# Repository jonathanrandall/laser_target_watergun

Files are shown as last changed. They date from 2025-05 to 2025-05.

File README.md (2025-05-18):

# laser_target_watergun
Laser Targetting watergun with esp32 cam and esp32 controlling the laser module.

[Explanatory video](https://youtu.be/Ic2vv7IDxok)

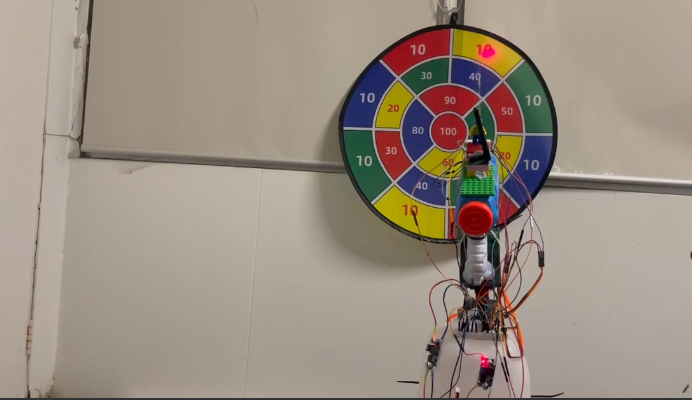
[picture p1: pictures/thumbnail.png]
Demo Video (https://youtu.be/Ic2vv7IDxok)


__Note:__ The __User_Setup.h__ file contains the configuration for the elecrow red display with the esp32. If using cheap yellow display need to set TFT_BL to -1. This would normally be set to 21, but pin 21 is held high by a pullup resistor, so the screen will still work.

## Directories:
__3d print files:__ This contains the files to 3d print the handset.

__schematics:__ This contains the schematics for the wiring for both the watergun side and the tft side

__tft_side_watergun_v2:__ The software for the tft side with the laser module attached

__watergun_side_v3:__ The software for the watergun side

__________________________________________

## Bill of Materials:

### Laser module with TFT screen
1. Laser Module. Note: laser module is not exaclty the same as laser pointer. Search amazon or aliexpress for "laser module". I'm using this one: [dot laser module](https://www.amazon.com.au/650nm-Laser-Module-Adjustable-Industrial/dp/B07PV4BWVH/)
2. TFT with esp32 connected. I'm using the elecrow red display, but you can use a cheap yellow display or a tft with an esp32. I'm using this one: [elecrow red display](https://www.elecrow.com/esp32-display-2-8-inch-hmi-display-spi-tft-lcd-touch-screen.html)
3. Push buttons x 2.
4. Pull up resistors X 2. I'm using 6.8 kohm, but anywhere from 5k to 15k should be ok.
5. 18650 battery and battery holder
6. Jumper wires, 3d printer,  hot glue, solder, etc...

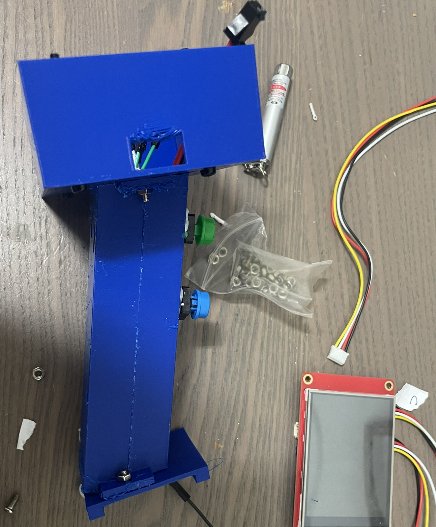
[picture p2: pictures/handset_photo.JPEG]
laser_module_handset


### Water gun side with camera
1. Esp32 cam. I'm using the AI thinker but any esp32 cam should be ok.
2. Electric wategun. The one I'm using isn't in production anymore. But any electric watergun that can fit easily onto a servo pan-tilt mechanism. Some might have an awkward shape at the bottom that makes it difficult. So keep this in mind. Also should have easy access to battery wiring should work.
3. High torque Servos x 2. I'm using 25kg/cm servos. You can get these from aliexpress.
4. Servo pan-tilt mechanism. One for size mg995 servo should work for the 25kg/cm servos from aliexpress. Don't get the smaller ones for the sg90 servos.
5. Buck converters X 2: one for the 6.5V supply for the servos and one for the 5V supply for the esp32 and watergun. I'm using the LM2596.
6. TB6612FNG motor controller.
7. Small breadboard.
8. Battery. I'm using a 2S lipo. But anything that works with the buck converters should be ok.
9. Jumper cables, hot glue, etc... 

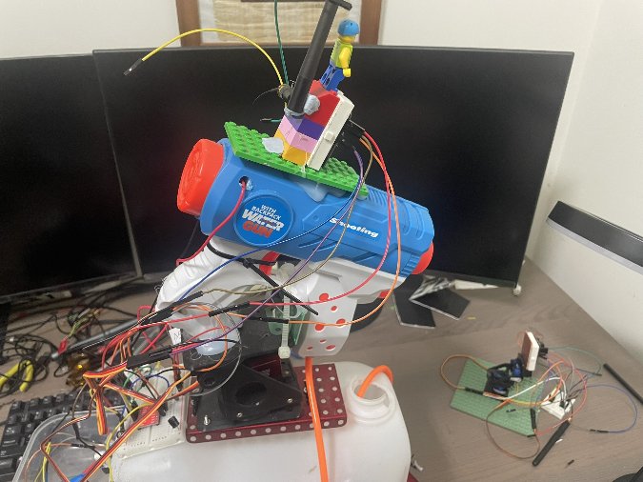
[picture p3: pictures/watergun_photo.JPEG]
watergun_side


previous videos on wategun are at:

[esp32 watergun](https://youtu.be/s5WNyXVWSS8)

[esp32 watergun with tracking](https://youtu.be/NK1wj7sDLNc)

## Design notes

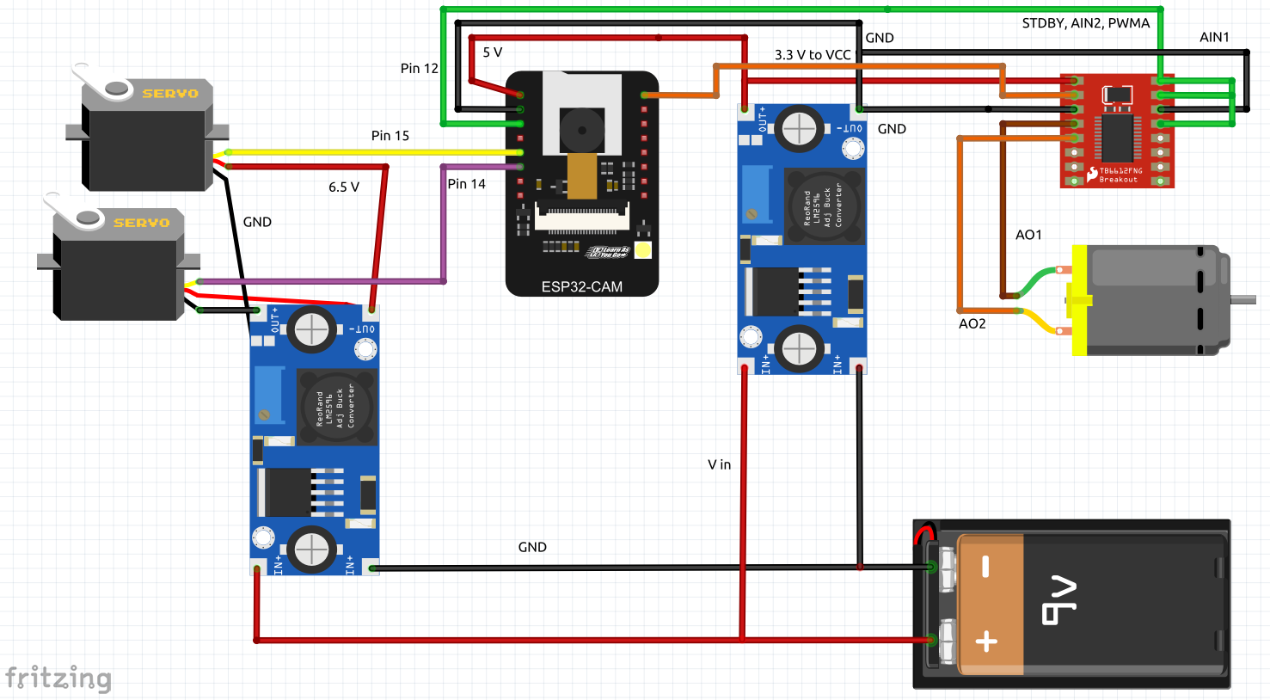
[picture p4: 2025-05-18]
schematics/watergun_schematic_labeled.png

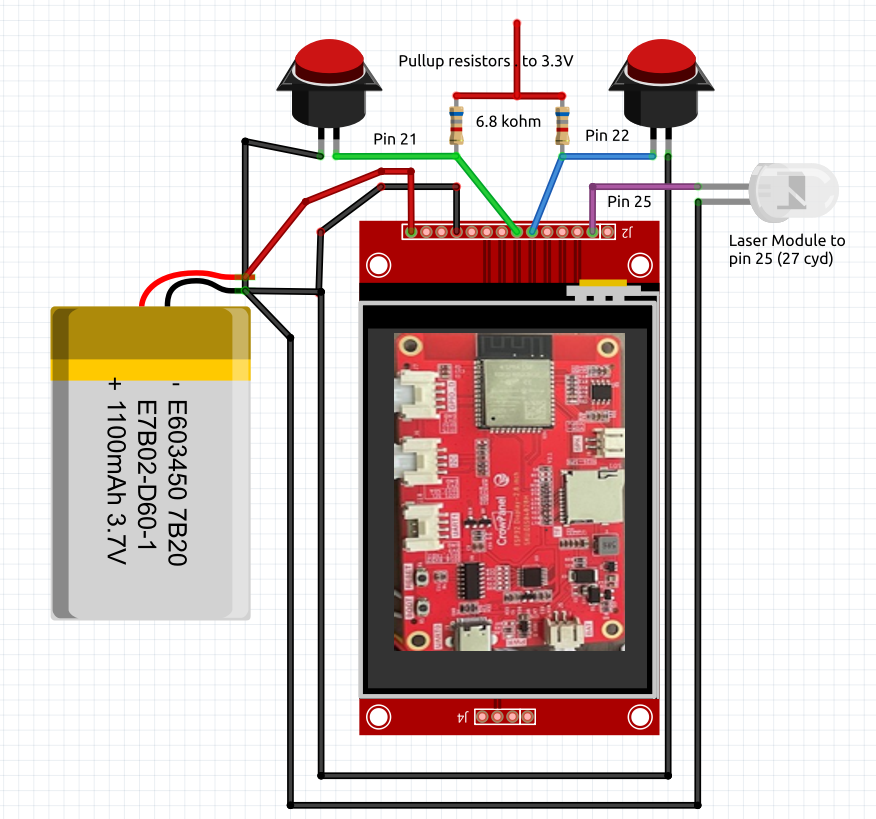
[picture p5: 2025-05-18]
schematics/tft_schematic_labeled_2.png

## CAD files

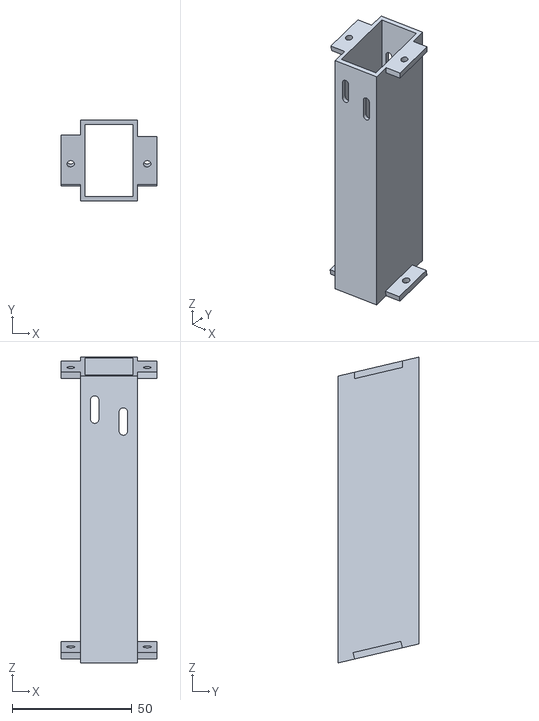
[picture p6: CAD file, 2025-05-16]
3d print files/handle_laser-Body.stl
40.0 x 34.0 x 128.0

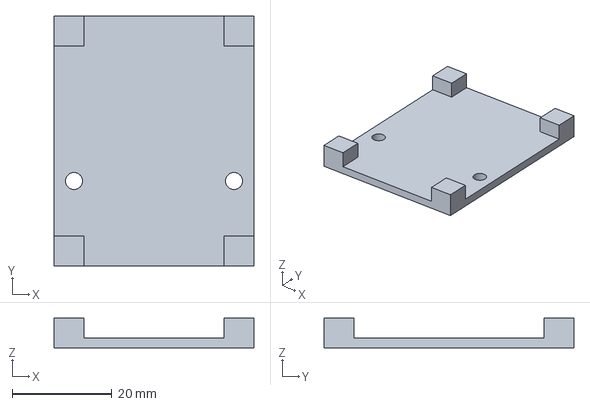
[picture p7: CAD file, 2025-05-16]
3d print files/handle_laser.FCStd
40.0 x 50.0 x 6.00 mm

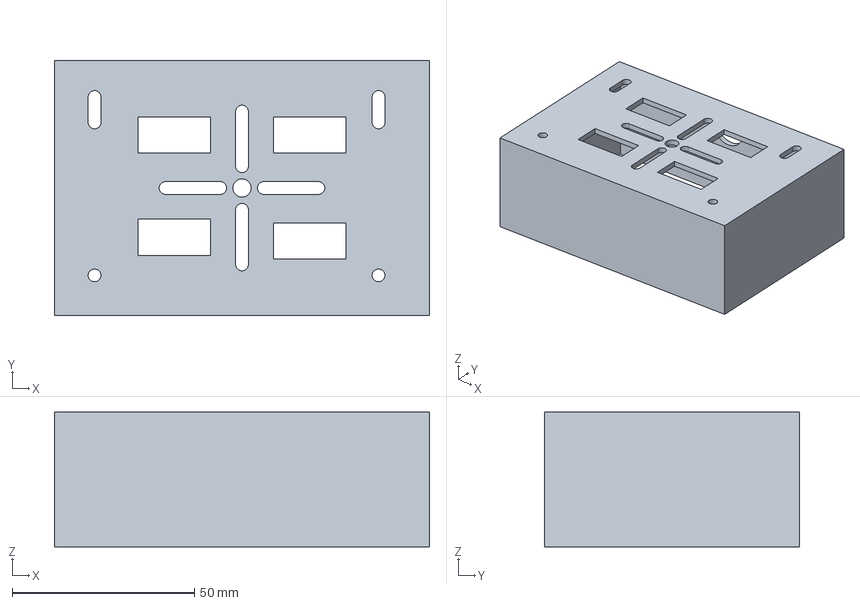
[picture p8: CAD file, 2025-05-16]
3d print files/box laser.FCStd
103.0 x 70.0 x 37.0 mm

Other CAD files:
3d print files/bottom_laser-Body.stl
3d print files/box_laser-Body.stl

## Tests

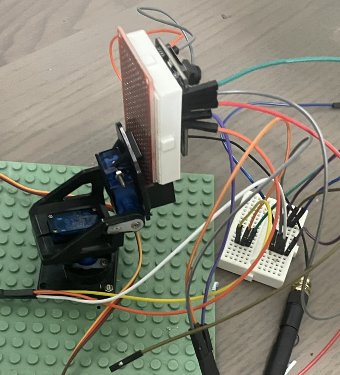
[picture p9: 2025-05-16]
pictures/test_rig_photo.JPEG

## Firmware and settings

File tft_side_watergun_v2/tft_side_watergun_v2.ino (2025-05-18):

#include <WiFi.h>
#include <TFT_eSPI.h>  // TFT library (make sure to include the correct library for your TFT display)
#include <HTTPClient.h>
#include <TJpg_Decoder.h>
#include "tft_stuff.h"




// const char* stream_url ="http://jonny-ubuntu.local:81/";// "http://192.168.4.1:81/stream";
// const char* stream_url ="http://192.168.4.1:81/stream";
// const char* stream_url = "http://rpizero.local:7123/stream11.mjpg";



// const char* ssid = "ESP32_CAM_AP";
// const char* password = "12345678";



#define PART_BOUNDARY "123456789000000000000987654321"
static const char* _STREAM_CONTENT_TYPE = "multipart/x-mixed-replace;boundary=" PART_BOUNDARY;
static const char* _STREAM_BOUNDARY = "\r\n--" PART_BOUNDARY "\r\n";
static const char* _STREAM_PART = "Content-Type: image/jpeg\r\nContent-Length ";//%u\r\n\r\n";

bool my_touch_read(uint16_t *x, uint16_t *y){
  bool touched = tft.getTouch(x,y);
  return touched;
}

bool tft_output(int16_t x, int16_t y, uint16_t w, uint16_t h, uint16_t* bitmap){
  if ( y >= tft.height() ) return 0;
  // tft.pushImage(x, y, w, h, bitmap);
  tft.pushImage(x, y, h, w, bitmap);
  return 1;
}

void processImage(uint8_t* image_data, size_t length) {
  // Serial.println("Processing full image...");
  TJpgDec.drawJpg(0, 0, (const uint8_t*)image_data, length);
  // Display or process the complete image here (e.g., render it on the TFT)
}

void drawJpeg(uint8_t* image_data, size_t length) {
  // Serial.println("Processing full image...");
  TJpgDec.drawJpg(0, 0, (const uint8_t*)image_data, length);
  // Display or process the complete image here (e.g., render it on the TFT)
}

void init_wifi_old()
{
  WiFi.mode(WIFI_STA);
  WiFi.begin(ssid, password);
  while (WiFi.status() != WL_CONNECTED) {
    delay(1000);
    Serial.println("Connecting to WiFi...");
  }
    Serial.println("");
    Serial.println("WiFi connected");
    Serial.println("IP address: ");
    Serial.println(WiFi.localIP());
    Serial.println("");
    return;

    
}

void init_wifi()
{
  WiFi.mode(WIFI_STA);
  
  // Attempt first SSID
  WiFi.begin(ssid, password);
  unsigned long startAttemptTime = millis();
  while (WiFi.status() != WL_CONNECTED && millis() - startAttemptTime < 10000) {
    delay(500);
    Serial.println("Connecting to primary WiFi...");
  }

  // If not connected after 5 seconds, try second SSID
  if (WiFi.status() != WL_CONNECTED) {
    Serial.println("Failed to connect to primary WiFi. Trying backup...");
    // WiFi.disconnect(true);
    // delay(80);
    WiFi.begin(ssid2, password2);
    startAttemptTime = millis();
    while (WiFi.status() != WL_CONNECTED && millis() - startAttemptTime < 5000) {
      delay(500);
      Serial.println("Connecting to backup WiFi...");
    }
  }

  // Final connection result
  if (WiFi.status() == WL_CONNECTED) {
    Serial.println("");
    Serial.println("WiFi connected");
    Serial.println("IP address: ");
    Serial.println(WiFi.localIP());
    Serial.println("");
  } else {
    Serial.println("Failed to connect to any WiFi network.");
  }
}


bool fire_done;
int unsigned long last_read_l;
int unsigned long last_read_f;
int unsigned long last_touch;

uint16_t px=0, py=0;
bool l_button_pushed, prev_l_button_pushed;
bool f_button_pushed, prev_f_button_pushed;
bool laser_on;
// HTTPClient http;
// WiFiClient* stream = nullptr;
void setup() {
  Serial.begin(115200);
  
  tft.init();
  tft.fillScreen(TFT_BLACK);  // Clear screen
  

  init_wifi();

    // Initialize the TFT screen
  tft.init();
  tft.setRotation(1);
  tft.setTextColor(TFT_WHITE,TFT_BLACK); 
  tft.fillScreen(TFT_BLACK);
  // tft.invertDisplay(true); //original and aliexpress but not elecros
  tft.setSwapBytes(true);
  tft.fillScreen(TFT_GREEN);
  delay(200);
  tft.fillScreen(TFT_BLACK);
  tft.setTextFont(4);
  tft.writecommand(ILI9341_GAMMASET); //Gamma curve selected for original one only but no aliexpress or elecrow.
  tft.writedata(2);
  delay(120);
  // tft.writecommand(ILI9341_GAMMASET); //Gamma curve selected
  tft.writedata(1);
  // analogWrite(21,64);

  TJpgDec.setJpgScale(1);
  TJpgDec.setCallback(tft_output);

  pinMode(laser_button, INPUT_PULLUP);
  pinMode(22, INPUT);
  pinMode(25, OUTPUT);

  xTaskCreatePinnedToCore(
       image_stream, /* Function to implement the task */
       "is",    /* Name of the task */
       1024*15,            /* Stack size in words */
       NULL,            /* Task input parameter */
       1,               /* Priority of the task */
       NULL,     /* Task handle. */
       1);              /* Core where the task should run */
 
//  xTaskCreatePinnedToCore(
//        laser_controls, /* Function to implement the task */
//        "lc",    /* Name of the task */
//        1024*5,            /* Stack size in words */
//        NULL,            /* Task input parameter */
//        1,               /* Priority of the task */
//        NULL,     /* Task handle. */
//        1);              /* Core where the task should run */
 

  // http.begin(stream_url);
  // int httpCode = http.GET();

  // if (httpCode == HTTP_CODE_OK) {
  //   stream = http.getStreamPtr();
  //   } else {
  //   Serial.printf("Failed to connect to stream, HTTP code: %d\n", httpCode);
  // }
  
  // Start the image stream
  // startStream();
  fire_done = false;
  last_read_l = millis();
  last_read_f = millis();
  last_touch = millis();

  prev_l_button_pushed = !digitalRead(laser_button); // digitalRead(laser_button);
  prev_f_button_pushed = !digitalRead(fire_button); //digitalRead(f_button);
  Serial.println("prev_l_button");
  Serial.println(prev_l_button_pushed);
  delay(1000);
  
  
}

// uint8_t *downloadBuffer = NULL;
//   int downloadBufferLength = 0;

//   uint8_t *mCurrentFrameBuffer = NULL;
//     size_t mCurrentFrameLength = 0;
//     size_t mCurrentFrameBufferLength = 0;
 void laser_controls(void *args){
  int unsigned long last_read_l;
  int unsigned long last_read_f;
  int unsigned long last_touch;
  last_read_l = millis();
  last_read_f = millis();
  last_touch = millis();
  uint16_t px=0, py=0;
  bool l_button_pushed, prev_l_button_pushed;
  bool f_button_pushed, prev_f_button_pushed;
  bool laser_on;
  prev_l_button_pushed = !digitalRead(laser_button); // digitalRead(laser_button);
  prev_f_button_pushed = !digitalRead(fire_button); //digitalRead(f_button);
  while (true){
    l_button_pushed = !digitalRead(laser_button); //high is off
    f_button_pushed = !digitalRead(fire_button); //high is off
    laser_on = digitalRead(laser);
    // Serial.print("prev l button");
    // Serial.println(prev_f_button_pushed);
    // Serial.print("l button");
    // Serial.println(l_button_pushed);
    if (millis() - last_read_l > 100 && !l_button_pushed && l_button_pushed!=prev_l_button_pushed){
      digitalWrite(laser, !laser_on); //toggle laser
      Serial.println("laser toggled");
      last_read_l = millis();
    }

    if (millis() - last_read_f > 1000 && laser_on && !f_button_pushed && f_button_pushed!=prev_f_button_pushed){
      Serial.println("target gotten");
      spray_target_with_water();
      last_read_f = millis();
      
      // sendMessage("target_get");
    }

    //squirt action

    if (!laser_on && f_button_pushed && !f_button_pushed!=prev_f_button_pushed){
      Serial.println("squirt");
      sendMessage("squirt");
      last_read_f = millis();
      
      // sendMessage("target_get");
    }

    /*
    //the my_touch_read needs a semaphore: TODO
    if (millis() - last_touch > 200 && my_touch_read(&px, &py)){
      sendMessage("reset_servos");
      last_touch = millis();
      Serial.println("reset_servos");
    }
    */
    prev_l_button_pushed = l_button_pushed;
    prev_f_button_pushed = f_button_pushed;
    delay(50);

  }
  
 }



void loop() {
  // vTaskDelete(NULL);
    l_button_pushed = !digitalRead(laser_button); //high is off
    f_button_pushed = !digitalRead(fire_button); //high is off
    laser_on = digitalRead(laser);
    // Serial.print("prev l button");
    // Serial.println(prev_f_button_pushed);
    // Serial.print("l button");
    // Serial.println(l_button_pushed);

    if (l_button_pushed){
      Serial.println("l button pushed");
    }
    
    if (millis() - last_read_l > 100 && l_button_pushed && l_button_pushed!=prev_l_button_pushed){
      digitalWrite(laser, !laser_on); //toggle laser
      Serial.println("laser toggled");
      last_read_l = millis();
    }
    
    

    if (millis() - last_read_f > 1000 && laser_on && f_button_pushed && f_button_pushed!=prev_f_button_pushed){
      Serial.println("target gotten");
      spray_target_with_water();
      last_read_f = millis();
      
      // sendMessage("target_get");
    }
    

    //squirt action

    if (!laser_on && f_button_pushed && f_button_pushed!=prev_f_button_pushed){
      Serial.println("squirt");
      String msg = sendMessage("squirt");
      Serial.println(msg);
      // last_read_f = millis();
    }
    
    /*
    //the my_touch_read needs a semaphore: TODO
    if (millis() - last_touch > 200 && my_touch_read(&px, &py)){
      sendMessage("reset_servos");
      last_touch = millis();
      Serial.println("reset_servos");
    }
    */
    prev_l_button_pushed = l_button_pushed;
    prev_f_button_pushed = f_button_pushed;
    
    delay(50);

 
}




void image_stream(void *args){
  HTTPClient http;
  WiFiClient* stream = nullptr;

  http.begin(stream_url);
  int httpCode = http.GET();

  if (httpCode == HTTP_CODE_OK) {
    stream = http.getStreamPtr();
    } else {
    Serial.printf("Failed to connect to stream, HTTP code: %d\n", httpCode);
  }
  
  while (true){
    if (stream && stream->connected()) {
    static bool in_image = false;
    static size_t content_length = 0;
    static uint8_t* imageBuffer = nullptr;

    if (stream->available()) {
      String line = stream->readStringUntil('\n');

      if (line.startsWith("--")) {
        in_image = false;
        if (imageBuffer) {
          drawJpeg(imageBuffer, content_length);
          free(imageBuffer);
          imageBuffer = nullptr;
        }
        content_length = 0;
      }

      if (line.startsWith("Content-Length: ")) {
        content_length = line.substring(15).toInt();
        imageBuffer = (uint8_t*)malloc(content_length);
        in_image = true;
      }

      if (in_image && imageBuffer) {
        size_t remaining = content_length;
        size_t bytes_read = 0;

        while (remaining > 0 && stream->available()) {
          bytes_read += stream->readBytes(imageBuffer + bytes_read, remaining);
          remaining = content_length - bytes_read;
        }

        if (remaining == 0) {
          in_image = false;
        }
      }
    }
  } else {
    Serial.println("Stream disconnected!");
    http.end();
    http.begin(stream_url);
    int httpCode = http.GET();
    if (httpCode == HTTP_CODE_OK) {
      stream = http.getStreamPtr();
    }
  }

  delay(10);
  } //while true

}

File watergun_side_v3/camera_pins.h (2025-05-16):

//#define CAMERA_MODEL_M5STACK_PSRAM
//#define CAMERA_MODEL_M5STACK_WITHOUT_PSRAM
//#define CAMERA_MODEL_M5STACK_PSRAM_B
//#define CAMERA_MODEL_WROVER_KIT



#define CAMERA_MODEL_AI_THINKER

#if defined(CAMERA_MODEL_WROVER_KIT)
#define PWDN_GPIO_NUM    -1
#define RESET_GPIO_NUM   -1
#define XCLK_GPIO_NUM    21
#define SIOD_GPIO_NUM    26
#define SIOC_GPIO_NUM    27

#define Y9_GPIO_NUM      35
#define Y8_GPIO_NUM      34
#define Y7_GPIO_NUM      39
#define Y6_GPIO_NUM      36
#define Y5_GPIO_NUM      19
#define Y4_GPIO_NUM      18
#define Y3_GPIO_NUM       5
#define Y2_GPIO_NUM       4
#define VSYNC_GPIO_NUM   25
#define HREF_GPIO_NUM    23
#define PCLK_GPIO_NUM    22

#elif defined(CAMERA_MODEL_ESP_EYE)
#define PWDN_GPIO_NUM    -1
#define RESET_GPIO_NUM   -1
#define XCLK_GPIO_NUM    4
#define SIOD_GPIO_NUM    18
#define SIOC_GPIO_NUM    23

#define Y9_GPIO_NUM      36
#define Y8_GPIO_NUM      37
#define Y7_GPIO_NUM      38
#define Y6_GPIO_NUM      39
#define Y5_GPIO_NUM      35
#define Y4_GPIO_NUM      14
#define Y3_GPIO_NUM      13
#define Y2_GPIO_NUM      34
#define VSYNC_GPIO_NUM   5
#define HREF_GPIO_NUM    27
#define PCLK_GPIO_NUM    25

#elif defined(CAMERA_MODEL_M5STACK_PSRAM)
#define PWDN_GPIO_NUM     -1
#define RESET_GPIO_NUM    15
#define XCLK_GPIO_NUM     27
#define SIOD_GPIO_NUM     25
#define SIOC_GPIO_NUM     23

#define Y9_GPIO_NUM       19
#define Y8_GPIO_NUM       36
#define Y7_GPIO_NUM       18
#define Y6_GPIO_NUM       39
#define Y5_GPIO_NUM        5
#define Y4_GPIO_NUM       34
#define Y3_GPIO_NUM       35
#define Y2_GPIO_NUM       32
#define VSYNC_GPIO_NUM    22
#define HREF_GPIO_NUM     26
#define PCLK_GPIO_NUM     21

#elif defined(CAMERA_MODEL_M5STACK_WIDE)
#define PWDN_GPIO_NUM     -1
#define RESET_GPIO_NUM    15
#define XCLK_GPIO_NUM     27
#define SIOD_GPIO_NUM     22
#define SIOC_GPIO_NUM     23

#define Y9_GPIO_NUM       19
#define Y8_GPIO_NUM       36
#define Y7_GPIO_NUM       18
#define Y6_GPIO_NUM       39
#define Y5_GPIO_NUM        5
#define Y4_GPIO_NUM       34
#define Y3_GPIO_NUM       35
#define Y2_GPIO_NUM       32
#define VSYNC_GPIO_NUM    25
#define HREF_GPIO_NUM     26
#define PCLK_GPIO_NUM     21

#elif defined(CAMERA_MODEL_AI_THINKER)
#define PWDN_GPIO_NUM     32
#define RESET_GPIO_NUM    -1
#define XCLK_GPIO_NUM      0
#define SIOD_GPIO_NUM     26
#define SIOC_GPIO_NUM     27

#define Y9_GPIO_NUM       35
#define Y8_GPIO_NUM       34
#define Y7_GPIO_NUM       39
#define Y6_GPIO_NUM       36
#define Y5_GPIO_NUM       21
#define Y4_GPIO_NUM       19
#define Y3_GPIO_NUM       18
#define Y2_GPIO_NUM        5
#define VSYNC_GPIO_NUM    25
#define HREF_GPIO_NUM     23
#define PCLK_GPIO_NUM     22

#else
#error "Camera model not selected"
#endif

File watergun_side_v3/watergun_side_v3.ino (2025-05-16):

/*********
  Rui Santos
  Complete instructions at https://RandomNerdTutorials.com/esp32-cam-projects-ebook/
  
  Permission is hereby granted, free of charge, to any person obtaining a copy of this software and associated documentation files.
  The above copyright notice and this permission notice shall be included in all copies or substantial portions of the Software.
*********/

#include "wifi_cam.h"


unsigned long st = 200;

void do_squirt(unsigned long st_ = 200){
  st = st_;
  digitalWrite(DRIVER_PIN, HIGH);
  squirt_water = true;
  squirt_tm = millis();
}

void setup() {
  WRITE_PERI_REG(RTC_CNTL_BROWN_OUT_REG, 0); //disable brownout detector
  
  Serial.begin(115200);
  // Serial.println("here");
  ////////////////////////////////////////////////////////////
  //changed here
  squirt_tm = millis();
  pinMode(DRIVER_PIN, OUTPUT);
  digitalWrite(DRIVER_PIN, LOW); //make sure motor is off
  ///////////////////////////////////////////////////////
  
  servo1.setPeriodHertz(50);    // standard 50 hz servo
  servo2.setPeriodHertz(50);    // standard 50 hz servo
  servoN1.attach(2, 1000, 2000);
  servoN2.attach(13, 1000, 2000);
  
  servo1.attach(SERVO_1, 1000, 2000);
  servo2.attach(SERVO_2, 1000, 2000);
  
  servo1Pos = 70; //top
  servo2Pos = 80;
  servo1.write(servo1Pos);
  servo2.write(servo2Pos);

  
  
  
  Serial.setDebugOutput(false);

  configure_camera();
  

  // Wi-Fi connection
  WiFi.mode(WIFI_AP_STA);
  WiFi.softAP(ssid, password);
  /*
  WiFi.begin(ssid, password);
  while (WiFi.status() != WL_CONNECTED) {
    delay(500);
    Serial.print(".");
  }
  */
  Serial.println("");
  Serial.println("WiFi connected");
  
  Serial.print("Camera Stream Ready! Go to: http://");
  Serial.println(WiFi.localIP());
  Semaphore_Controls = xSemaphoreCreateMutex();
  pinMode(laser_pin, OUTPUT);
  digitalWrite(laser_pin, HIGH);
  pinMode(DRIVER_PIN, OUTPUT);
  digitalWrite(DRIVER_PIN, LOW);
  // Start streaming web server
  startCameraServer();
  servo1.write(servo1Pos);
  servo2.write(servo2Pos);
}

void loop() {

  if (move_servos_inloop){
    Serial.println("in loop");
    Serial.println(x_move_calibrate);
    Serial.println(y_move_calibrate);
    adjust_servos((int) x_move_calibrate, (int) y_move_calibrate);
    delay(500);
    digitalWrite(DRIVER_PIN, HIGH);
    delay(400);
    digitalWrite(DRIVER_PIN, LOW);
    move_servos_inloop = false;
    // do_squirt();
  }

  if(squirt_water && (millis()-squirt_tm)>st){
    digitalWrite(DRIVER_PIN, LOW);
    squirt_water = false;
  }

 delay(50);
}

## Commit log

2025-05-16 update code files
    [bottom_laser-Body.stl, box laser.FCStd, box_laser-Body.stl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]
2025-05-18 update files
    [rpi_zero_holder-Body.stl, rpi_zero_holder-Body001.stl, rpi_zero_holder.FCStd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]
